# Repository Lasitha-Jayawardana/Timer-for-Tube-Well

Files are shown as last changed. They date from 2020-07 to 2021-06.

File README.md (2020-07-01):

# Timer-for-Tube-Well
Automated water filling system with dual motor including Tube well and upper tank.

# Tips
This include Arduino file and Eagle cad PCB project. And also Camout and CNC milling files are in here with.

First tank fill from the tube well using On and Off timer for tube well motor.
Second Tank fill from first tank by different motor.
Water level is measured by Sona Sensor in each tank. 
After full filled each tank, each motors are temporaly wait till water level goes down.

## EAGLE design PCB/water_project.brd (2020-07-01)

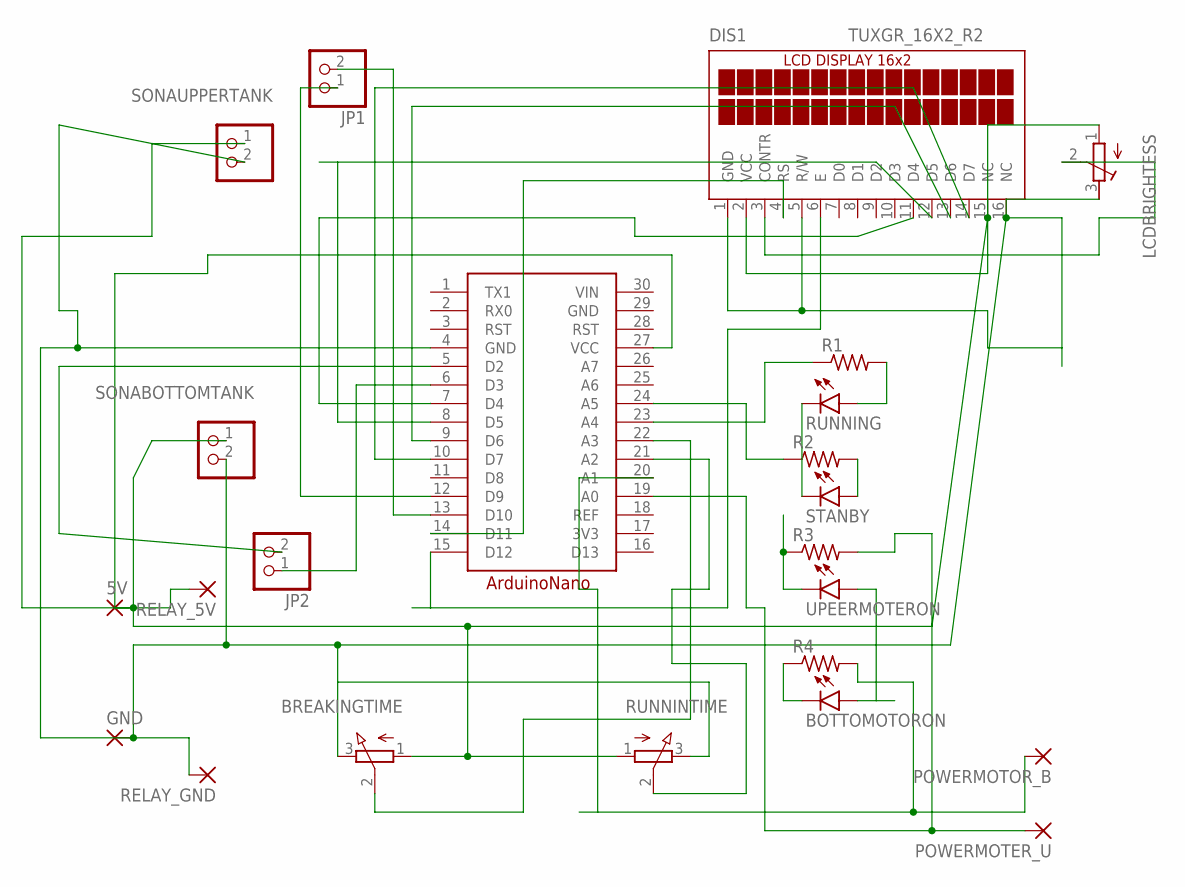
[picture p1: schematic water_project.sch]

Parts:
5V: 3,17/1,3
A1: ARDUINONANO
BOTTOMOTORON: LEDSFH480; SFH480
BREAKINGTIME: 3RP/1610N
DIS1: TUXGR_16X2_R2
GND: 3,17/1,3
JP1, JP2: PINHD-1X2; 1X02
LCDBRIGHTESS: R-TRIMM3339P; RTRIM3339P
POWERMOTER_U: 3,17/1,3
POWERMOTOR_B: 3,17/1,3
R1, R2, R3, R4: R-US_0207/7; 0207/7
RELAY_5V: 3,17/1,3
RELAY_GND: 3,17/1,3
RUNNING: LEDSFH480; SFH480
RUNNINTIME: 3RP/1610N
SONABOTTOMTANK: PINHD-1X2; 1X02
SONAUPPERTANK: PINHD-1X2; 1X02
STANBY: LEDSFH480; SFH480
UPEERMOTERON: LEDSFH480; SFH480

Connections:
3V3: A1.17 (3V3)
ECHO: A1.13 (D10), JP1.2
ECHO1: A1.5 (D2), JP2.2
GND: A1.4 (GND), A1.29 (GND), BREAKINGTIME.3 (E), DIS1.1 (GND), DIS1.5 (R/W), DIS1.16 (NC), GND.1, LCDBRIGHTESS.3 (E), RELAY_GND.1, RUNNINTIME.3 (E), SONABOTTOMTANK.2, SONAUPPERTANK.2
unnamed: R1.2, RUNNING.A
unnamed: R2.2, STANBY.A
unnamed: BOTTOMOTORON.K (C), R4.1
unnamed: DIS1.3 (CONTR), LCDBRIGHTESS.2 (S)
unnamed: A1.7 (D4), DIS1.11 (D4)
unnamed: A1.8 (D5), DIS1.12 (D5)
unnamed: A1.9 (D6), DIS1.13 (D6)
unnamed: A1.10 (D7), DIS1.14 (D7)
unnamed: RUNNING.K (C), STANBY.K (C)
unnamed: A1.14 (D11), DIS1.4 (RS)
unnamed: A1.15 (D12), DIS1.6 (E)
unnamed: A1.21 (A2), RUNNINTIME.2 (S)
unnamed: A1.22 (A3), BREAKINGTIME.2 (S)
unnamed: A1.19 (A0), POWERMOTER_U.1, R3.2
unnamed: A1.20 (A1), POWERMOTOR_B.1, R4.2
unnamed: A1.23 (A4), R1.1
unnamed: A1.24 (A5), R2.1
unnamed: R3.1, UPEERMOTERON.K (C)
REF: A1.18 (REF)
TRIG: A1.12 (D9), JP1.1
TRIG1: A1.6 (D3), JP2.1
VCC: 5V.1, A1.27 (VCC), BOTTOMOTORON.A, BREAKINGTIME.1 (A), DIS1.2 (VCC), DIS1.15 (NC), LCDBRIGHTESS.1 (A), RELAY_5V.1, RUNNINTIME.1 (A), SONABOTTOMTANK.1, SONAUPPERTANK.1, UPEERMOTERON.A
VIN: A1.30 (VIN)

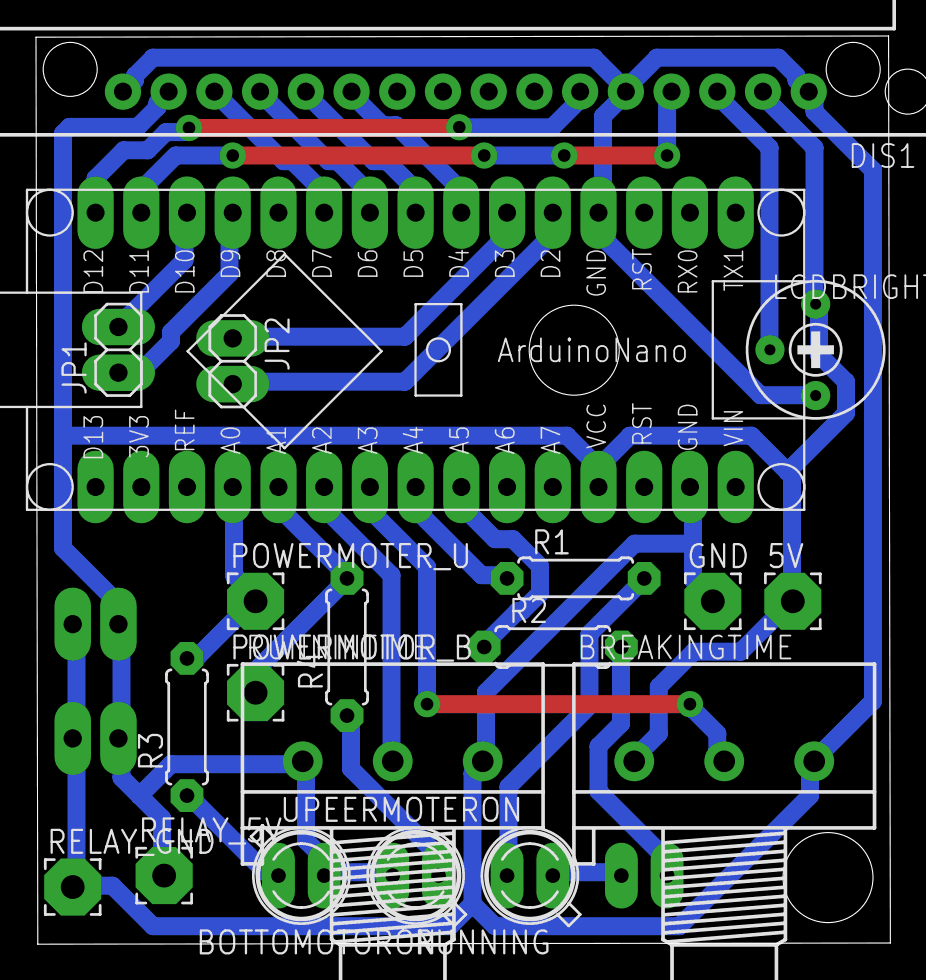
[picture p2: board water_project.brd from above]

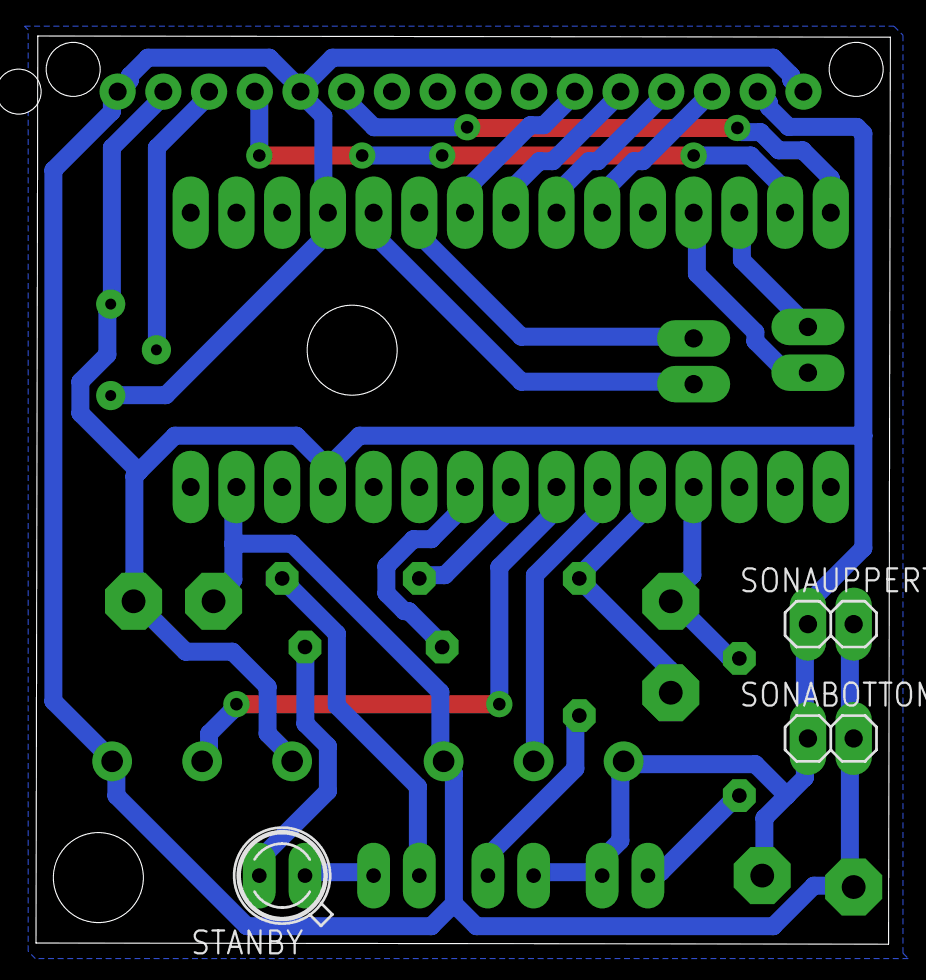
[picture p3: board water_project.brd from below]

Board: 2 copper layers, 47.5 x 50.5 mm, 23 parts (3 on the bottom side), 24 nets.

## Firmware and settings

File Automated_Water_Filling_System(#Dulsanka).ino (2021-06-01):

#include <LiquidCrystal.h> // includes the LiquidCrystal Library

LiquidCrystal lcd(11, 12, 4, 5, 6, 7); // Creates an LCD object. Parameters: (rs, enable, d4, d5, d6, d7)
const int TtrigPin = 9;
const int TechoPin = 10;
const int BtrigPin = 3;
const int BechoPin = 2;

const int OnTimePin = A2;
const int OffTimePin = A3;

const int RuningledPin = A4;
const int StanbyledPin = A5;

/*tank level for display persentage*/
const int TankBu = 25;//cm
const int TankBl = 100;
const int TankTu = 20;//cm
const int TankTl = 250;

/*tank level for automated process*/
const int Bu = 25;//cm
const int Bl = 40;
const int Tu = 40;
const int Tl = 180;

int emergency = 0;
int flag = 0;
int modeB = 0;
volatile unsigned long oldtime = 0;

const int motorpowerT = A0;
const int motorpowerB = A1;
int motorstateB = 1;
int motorstateT = 1;

unsigned long runing_time = 10;
unsigned long breaking_time = 9;
unsigned long old_rvalue = 0;
unsigned long old_bvalue = 0;

long duration;
int TdistanceCm, BdistanceCm;

int Ttemp = 0;
int Btemp = 0;

void map_runing_time() {
  runing_time = map(analogRead(OnTimePin), 0, 1023, 0, 9) * 30;
  if (runing_time != old_rvalue) {
    old_rvalue = runing_time;
    if (!emergency) {
      lcd.setCursor(4, 1);
      lcd.print("   ");
      lcd.setCursor(4, 1);
      lcd.print(runing_time);
    }
  } else {

  }
}

void map_breaking_time() {
  breaking_time = map(analogRead(OffTimePin), 0, 1023, 0, 9) * 5;
  if (breaking_time != old_bvalue ) {
    old_bvalue =  breaking_time;
    if (!emergency) {
      lcd.setCursor(12, 1);
      lcd.print("   ");
      lcd.setCursor(12, 1);
      lcd.print(breaking_time);
    }
  } else {

  }
}


void gettoptanklevel() {
  duration = 0;
  digitalWrite(TtrigPin, LOW);
  delayMicroseconds(2);
  digitalWrite(TtrigPin, HIGH);
  delayMicroseconds(10);
  digitalWrite(TtrigPin, LOW);
  duration = pulseIn(TechoPin, HIGH);
  TdistanceCm = duration * 0.034 / 2;
  //  Serial.print("Top : ");
  //Serial.println(TdistanceCm);
}

void getbottomtanklevel() {
  duration = 0;
  digitalWrite(BtrigPin, LOW);
  delayMicroseconds(2);
  digitalWrite(BtrigPin, HIGH);
  delayMicroseconds(10);
  digitalWrite(BtrigPin, LOW);
  duration = pulseIn(BechoPin, HIGH);
  BdistanceCm = duration * 0.034 / 2;
  //Serial.print("bottom : ");
  //Serial.println(BdistanceCm);

}
void motorTon() {
  digitalWrite(motorpowerT, LOW);
  motorstateT = 1;
}
void motorToff() {
  digitalWrite(motorpowerT, HIGH);
  motorstateT = 0;
}

void motorBon() {
  digitalWrite(motorpowerB, LOW);
  motorstateB = 1;
}
void motorBoff() {
  digitalWrite(motorpowerB, HIGH);
  motorstateB = 0;
}
void setup() {
  Serial.begin(9600);
  lcd.begin(16, 2); //Initializes the interface to the LCD screen, and specifies the dimensions (width and height) of the display
  pinMode(TtrigPin, OUTPUT);
  pinMode(TechoPin, INPUT);
  pinMode(BtrigPin, OUTPUT);
  pinMode(BechoPin, INPUT);
  motorToff();
  motorBoff();
  pinMode(motorpowerT, OUTPUT);
  pinMode(motorpowerB, OUTPUT);
  pinMode(StanbyledPin, OUTPUT);
  pinMode(RuningledPin, OUTPUT);

  pinMode(OnTimePin, INPUT);
  pinMode(OffTimePin, INPUT);
  map_runing_time();
  map_breaking_time();

  if (runing_time  > 235 and breaking_time > 35) {
    emergency = 1;
    runing_time = 90;
    breaking_time = 20;
  } else {
    emergency = 0;
  }

  if (emergency) {
    digitalWrite(RuningledPin, HIGH );
    digitalWrite(StanbyledPin, HIGH );
    lcd.clear();

    lcd.setCursor(0, 0);

    lcd.print(" Emergency Mode ");

    lcd.setCursor(4, 1);
    lcd.print("   ");
    lcd.setCursor(4, 1);
    lcd.print(runing_time);
    lcd.setCursor(12, 1);
    lcd.print("   ");
    lcd.setCursor(12, 1);
    lcd.print(breaking_time);

    delay(500);
  } else {
    lcd.setCursor(0, 0); // Sets the location at which subsequent text written to the LCD will be displayed
    lcd.print("T1: ");
    lcd.setCursor(8, 0); // Sets the location at which subsequent text written to the LCD will be displayed
    lcd.print("T2: ");


  }
  lcd.setCursor(0, 1); // Sets the location at which subsequent text written to the LCD will be displayed
  lcd.print("RT: ");
  lcd.setCursor(8, 1); // Sets the location at which subsequent text written to the LCD will be displayed
  lcd.print("BT: ");


}

void TaskB() {
  if (!emergency) {
    map_runing_time();
    map_breaking_time();
    if (BdistanceCm <= Bu and modeB == 1) {
      modeB = 0;
      if (motorstateB != 0) {
        motorBoff();
      }
    } else if (BdistanceCm >= Bl and modeB == 0) {
      modeB = 1;
    }
  }



  if (modeB == 1 or emergency == 1 ) {

    if (oldtime + runing_time * 1000 < millis() and flag == 0) {
      flag = 1;
      oldtime = millis();
      motorBoff();
    } else if (oldtime + breaking_time * 1000 * 60 < millis() and flag == 1) {
      flag = 0;
      oldtime = millis();
      motorBon();
    }
  }

}


void TaskT() {
  if (TdistanceCm <= Tu) {

    if (motorstateT != 0) {
      motorToff();
    }
  } else if (TdistanceCm >= Tl ) {
    if (motorstateT != 1) {
      motorTon();
    }
  }

}


void loop() {




  if (!emergency) {
    gettoptanklevel();
    int Tpresentage = float((TdistanceCm - TankTu) * 100) / float((TankTl - TankTu));
    Serial.println(TdistanceCm);
    if ( Ttemp != Tpresentage) {
      Ttemp = Tpresentage;
      lcd.setCursor(11, 0);
      lcd.print("     ");
      lcd.setCursor(11, 0);
      lcd.print(Tpresentage);
      lcd.print("%");
    }
    delay(100);

    getbottomtanklevel();
    int Bpresentage = float((BdistanceCm - TankBu) * 100) / float((TankBl - TankBu));

    if ( Btemp != Bpresentage) {
      Btemp = Bpresentage;
      lcd.setCursor(3, 0);
      lcd.print("     ");
      lcd.setCursor(3, 0);
      lcd.print(Bpresentage);
      lcd.print("%");
    }
    delay(100);

    if (modeB == 1) {
      digitalWrite(RuningledPin, HIGH );
      digitalWrite(StanbyledPin, LOW );
    } else {
      digitalWrite(RuningledPin, LOW);
      digitalWrite(StanbyledPin, HIGH);
    }

  } else {
    delay(200);
  }

  //TaskT();
  TaskB();

}
